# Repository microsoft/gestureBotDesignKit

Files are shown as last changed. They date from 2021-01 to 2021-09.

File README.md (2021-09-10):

##  [Microsoft Applied Robotics Research Library](https://microsoft.github.io/AppliedRoboticsResearchLibrary/)
### Open Source Samples for Service Robotics
  

# gestureBot Design Kit
Welcome! This gestureBot Design Kit repository  contains all the information needed to build both a virtual and physical desktop companion robot. Along with other tools in the Labanotation Suite, the gestureBot can be used to create and edit gestures documented in the Labanotation format and see them performed by a robot.  

A Windows 10 PC is required to run the software and the virtual robot. The physical robot can be built using a desktop 3D-printer and about **$350(USD)** in electronic servos and parts.

The kit contains a browser-based simulated robot with control software based on the [Robotis XL](https://www.robotis.us/dynamixel-xl-320/) series of servo motors. To construct a physical robot, it provides models for 3D-printable body-parts, a parts-list and purchase links for electronic components, and step-by-step assembly instructions. No soldering is required, but some manual skill is needed to mate small electronic connectors, manipulate small plastic rivets, and install miniature metal screws to assemble the body components.

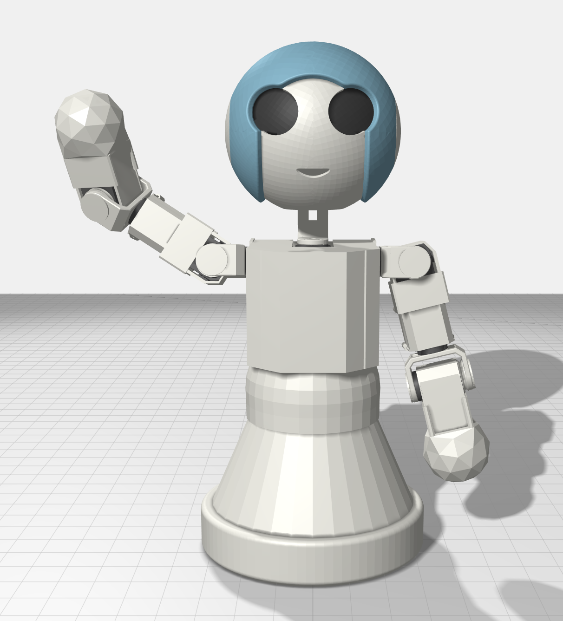
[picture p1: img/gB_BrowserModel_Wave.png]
Browser Model Wave


## What is the gestureBot and who might be interested in using this kit?
The gestureBot is a semi-humanoid service-robot capable of mimicking human gestures. Its purpose is to support research and education in the field of ***Human-Robot-Interaction (HRI)***. Its function is to physically and virtually render gestures stored in a digital Labanotation format. The designation "semi-humanoid" means that it has some but not all of the limbs and joints of a human form. The designation **"service-robot"** refers to a requirement that is designed to safely operate directly with humans, as opposed to an **"industrial-robot"** that usually repeats tasks within a cordoned-off safety zone. The gestureBot was adapted from a project originally created by interns working for Microsoft Research Asia. We've built on their work and put together this design kit to help students learn with a fun hand's-on project that provides exposure to key technologies used in service-robotics. Researchers in the field of HRI can use the kit to support experimentation in the use of gestures to enhance robot-to-human comunication.

No matter where your interest lies, we hope you find the gestureBot Design Kit a fun and easy way to work and learn in the field of robotics.

# How It Works
## System Diagram
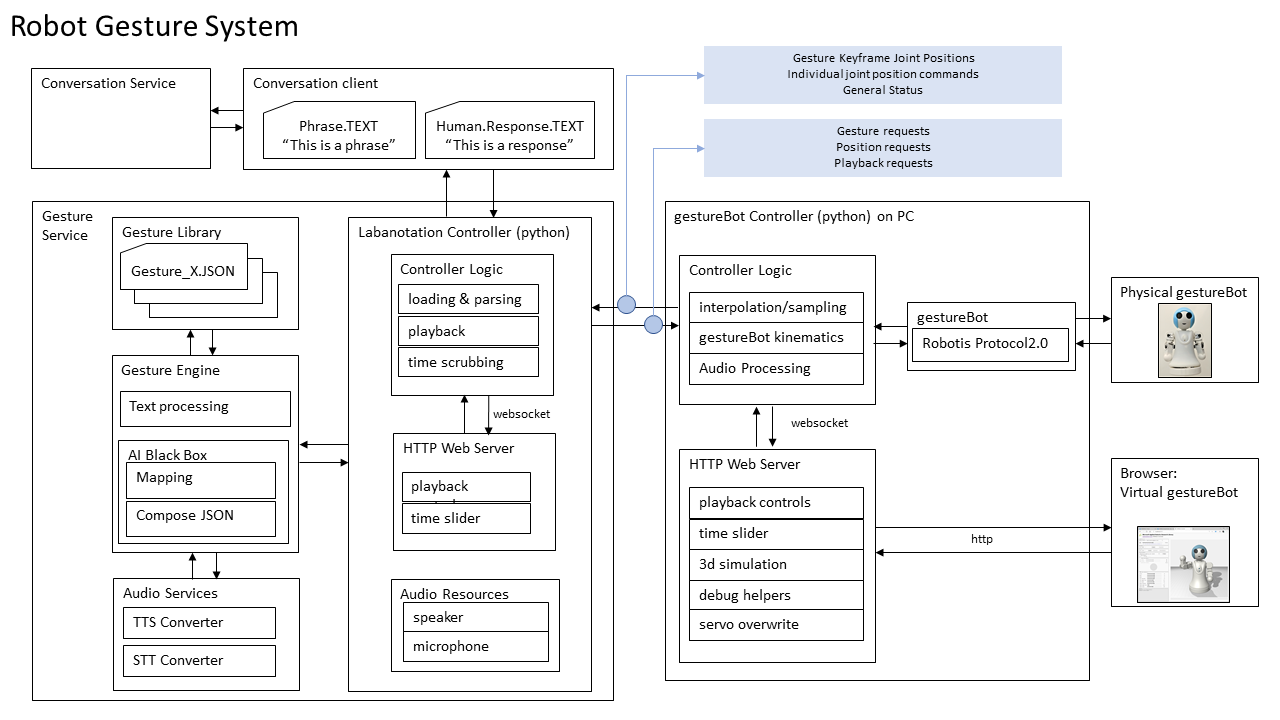
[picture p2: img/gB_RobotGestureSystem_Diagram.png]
gestureBot System Diagram


## System Modules:

### **Gesture Service**

#### **Labanotation Controller**
The Labanotation Controller reads .json files containing gestures described in Labanotation format, which are recordings of human gestural movements reduced to significant keyframes consisting of sequenced joint position and movement timing goals. Gesture selection and loading, as well as joint positional movements and their durations contained in the gestures, are requested by and sent to the gestureBot Controller module. The keyframes can also be transmitted under the control of simple play/pause commands and a scrubbing timeline with a browser-based UI available on **http port 8000**.

#### **Gesture Library**
The [**Gesture Library**](./src/Labanotation/README.md) is a database of gesture-concept pairs expressed in Labanotation format and stored as .json files. The data is directly accessed by the Gesture Engine.  The library includes a complete listing of the sample database including a video clip of each gesture performed by the gestureBot.

#### **Gesture Engine**
For humanoid robot performance, the Gesture Engine contains a software module constructed with Python and Google's neural network [**word2vec**](https://code.google.com/archive/p/word2vec/#!). It receives text phrases from the Labanotation Controller as input and returns corresponding gestures. Sample text phrases and gesture-concept pairs contained in the Gesture Library can be previewed by the system with a browser-based UI available on **http port 8002**.

### **gestureBot Controller**
The gestureBot Controller requests from the Labanotation Controller gestures to be loaded and played. Optionally, it will interpolate and insert interstitial keyframes between Labanotation keyframes in a gesture at a selectable sampling rate. It transforms goal positions and times contained in the keyframes into joint servo commands calculated using information specific to the the gestureBot's physical characteristics. It animates both the real and models of the robot using the servo commands and a library of virtual model assets. Finally, it provides a browser-based user interface on **http port 8001** for:
*   Selecting a Gesture-Concept .json input file for rendering
*   Optionally setting a sample rate for interstitial keyframe extrapolations between Labanotation keyframes
*   Optionally showing keyframe goal positions with "bone segments" within the browser-hosted model
*   Optionally hide cover components in the browser-hosted model
*   Direct override control for individual servos in the gestureBot
*   Previewing a gesture or movement in a simple simulator
*   Reporting application status with console messages

### **Real and Simulated gestureBots**
Both physical gestureBots and virtual models hosted in a browser connect to the gestureBot controller and receive movement commands as servo-control packets. The packets adhere to the [Robotis Dynamixel 2.0 Protocol](https://emanual.robotis.com/docs/en/dxl/x/xl320/). A packet is sent for each Labanotation and interstitial keyframe transmitted by the gestureBot Controller and contains individual goal positions and movement durations for each servo in the gestureBot.

# Install, Build and Run
- [Software Installation Instructions ](./src/Samples/gestureService_w2v/README.md) for the controller applications
- [Step-by-Step Instructions ](./hardware/README.md) for constructing a physical gestureBot

# Contributing
We think the gestureBot can be made to do much more than render gestures and we hope you will help it evolve! We have designed the hardware and software to be easy to understand and modify.
- Please read our [short and sweet coding guidelines](coding_guidelines.md).
- For big changes such as adding new feature or refactoring, [file an issue first](https://github.com/Microsoft/gestureBotDesignKit/issues).
- Use our [recommended development workflow](dev_workflow.md) to make changes and test it.
- Use [usual steps](https://akrabat.com/the-beginners-guide-to-contributing-to-a-github-project/) to make contributions just like other GitHub projects. If you are not familiar with Git Branch-Rebase-Merge workflow, please [read this first](http://shitalshah.com/p/git-workflow-branch-rebase-squash-merge/).

## Checklist
- Use same style and formatting as rest of code even if it's not your preferred one.
- Change any documentation that goes with code changes.
- Do not include OS specific header files or new 3rd party dependencies.
- Keep your pull request small, ideally under 10 files.
- Don't don't include large binary files.
- When adding new includes, make sure the dependency is absolutely necessary.
- Rebase your branch frequently with master (once every 2-3 days is ideal).
- Make sure your code compiles on Windows, Linux and OSX.

## FAQ

*   **Q** *Who should I contact regarding this repository?*

*   **A** Please create a Github issue or email [robosupp@microsoft.com](mailto:robosupp@microsoft.com) with any questions or feedback.

*   **Q** *How challenging is this project for children?*

*   **A** We think it depends on the child and how much support they receive!  We'd love to attract kids who love Minecraft and/or Legos, but we've shaped this project to be easily accessible to high-school and college STEM faculty looking for affordable lab projects, academic HRI researchers, and casual hobbyists.

*   **Q** *How does this project relate to Artificial Intelligence (AI)?*

*   **A** Physics-based simulation of real robots in virtual environments opens the door for the use of AI "brain" training using Reinforcement Learning tool-chains such as [Microsoft Bonsai](https://bons.ai).

## Citation

If you want to cite this work, please use the following bibtex code

```
@Article{Ikeuchi2018,
author="Ikeuchi, Katsushi
and Ma, Zhaoyuan
and Yan, Zengqiang
and Kudoh, Shunsuke
and Nakamura, Minako",
title="Describing Upper-Body Motions Based on Labanotation for Learning-from-Observation Robots",
journal="International Journal of Computer Vision",
year="2018",
month="Dec",
day="01",
volume="126",
number="12",
pages="1415--1429",
issn="1573-1405",
doi="10.1007/s11263-018-1123-1",
url="https://doi.org/10.1007/s11263-018-1123-1"
}
```

If you want to learn more about creating good readme files then refer the following [guidelines](https://docs.microsoft.com/en-us/azure/devops/repos/git/create-a-readme?view=azure-devops). You can also seek inspiration from the below readme files:
- [ASP.NET Core](https://github.com/aspnet/Home)
- [Visual Studio Code](https://github.com/Microsoft/vscode)
- [Chakra Core](https://github.com/Microsoft/ChakraCore)

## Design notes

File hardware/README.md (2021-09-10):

##  [Microsoft Applied Robotics Research Library](https://microsoft.github.io/AppliedRoboticsResearchLibrary/)
### Open Source Samples for Service Robotics
  

# gestureBot Construction Guide

The gestureBot is adapted from the [**Mini**](https://www.robotis.us/robotis-mini-intl/) robot kit from [**Robotis, Inc**](https://www.robotis.us) and the MSRAbot project created by interns at Microsoft Research Asia.
The information on this page will guide you through [**purchasing**](#purchased-parts) and [**printing**](#3d-printed-parts) parts, as well as [**step-by-step assembly**](#step-by-step-instructions) of the gestureBot.

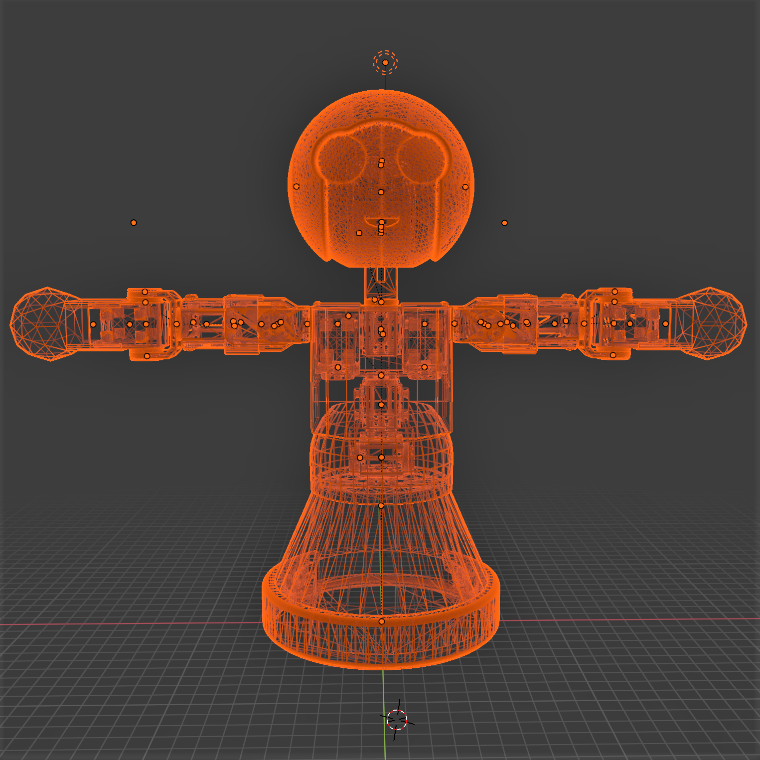
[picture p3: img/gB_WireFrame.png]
gestureBot wireframe


# Before you begin...
If you have experience in 3D printing and electronic assembly, we hope that you find this project relatively simple and straight-forward.  Once the parts are in-hand, the time required to complete the project won't be much more than it takes to print the 3D models.

If you are not experienced in these areas, one of the first things you'll learn is that desktop ***3D-printers are not a good source of instant gratification!***  Even the smallest of the models contained in this kit will take several hours to print, while some of the larger models take more than half a day.  With those time requirements in mind, we broke the procedures down into work sessions that fit along with the 3D print operations. Alternatively, a class of 5-10 students taking on this project might be successful with serial use of a single 3D printer and meeting once-a-week to perform the other assembly tasks.

An important feature of these instructions is their sequence. Following the steps in the sessions ***in order*** is key to preventing the need to disassemble an assembly in order to have access to cable pathways or screw and rivet holes.

# ***Safety Alert:***

We've found that a key to success in building this and other projects using 3D-printed plastic parts is to ***know your own strength***. Human hands can be more than strong enough to damage or destroy plastic parts, especially when muscle force is amplified by the leverage provided by a tool. For example, gripping a screwdriver with your fingers instead of the palm of your hand will limit the torque force you can apply with your muscles when driving a metal screw into a plastic servo horn (wheel). ***When applying muscle force with a tool against a plastic part, being aware of where the stationary force from your hand, body, or workbench is pushing back against your tool can avoid suddenly breaking the part and possibly causing injury.*** It is also helpful to use vision as well as force when tightening a screw. Paying attention to the closing gaps when turning a screw can help avoid stripping threads in the plastic and will make for stronger connections. A famous book that discusses this concept of "mechanic's feel" as well as other challenges in life is [***Zen and the Art of Motorcycle Maintenance: An Inquiry into Values***](https://hpb.com/products/zen-and-the-art-of-motorcycle-maintenance-an-inquiry-into-values-9780060589462) by Robert M. Persig.

## Requirements
Here are the physical things you'll need to build and use your gestureBot:

### PC
- x64 CPU
- Microsoft Windows 10
- USB3 port (USB2 can work in some cases)

### Tools
- 3D printer (we use an [Ultimaker3](https://ultimaker.com/3d-printers/ultimaker-3) with PLA filament)
- [Wire Stripper/Cutter](https://vetco.net/products/16awg-32awg-wire-stripper-cutter/plat-15005c)
- [small Phillips screwdriver (PH0)](https://vetco.net/products/general-tools-712010-precision-screwdriver-phillips-0)
- [small flat-blade screwdriver (2mm)](https://vetco.net/products/)
  - Alternative Screwdrivers:
    - [5 in 1 Precision Screwdriver](https://vetco.net/products/general-tools-spc606-jewelers-screwdriver-set-of-5)
    - [16 in 1 Precision Screwdriver](https://vetco.net/products/16-in-1-precision-screwdriver-set)
- pen and light-colored tape for labeling servo ID's

### Optional but Helpful Tools
- [Rivet Tool](https://www.robotis.us/tool-stl/)
- needle-nose pliers
- [Magnet (for easier screw driving)](https://vetco.net/products/3-4-round-magnet/son-pm550)
- 3mm drill bit, variable speed drill
- [3D-printing cleanup tools](https://www.matterhackers.com/articles/tools-of-the-trade-to-make-your-life-as-a-3d-print-master-much-simpler). A swivel deburring tool is especially useful.

## Parts List
### Purchased Parts
|**ID**|**Qty**|**Name & Purchase Link**|** . **|
|:--:|:--:|:---:|:---:|
|P1|12|[Robotis XL-320 Servo Motors (includes short connection cable)](https://www.robotis.us/dynamixel-xl-320/)||
|P2|1|[USB3 Hub with Power Supply](https://vetco.net/products/4-port-powered-usb-3-0-hub/vupn615)||
|P3|1|[Robotis OpenCM9.04c Servo Control Circuit Board](https://www.robotis.us/opencm9-04-c-with-onboard-xl-type-connectors/)|
|P4|1|[USB Terminal Block](https://vetco.net/products/usb-a-male-to-screw-terminal-breakout/cv051)|
|P5|1|[Short USB Cable (USB-A to USB-Micro)](https://vetco.net/products/usb-a-to-micro-usb-90-angle/)||
|P6|2|[Long (19cm) Servo Connection Cables](https://www.robotis.us/robot-cable-3p-xl-190mm-5pcs/)||
|P7|1|[6mm Plastic Rivets, (40) short (2-step) and (10) long (3-step)](https://www.robotis.us/robotis-mini-rivet-set/)||
|P7 (alternate)|1|[6mm Plastic Rivets (weaker but lower-cost, variety of colors)](https://www.robotis.us/rivet-set-rs-10/)||
|P8|1|[Screw Set](https://www.robotis.us/robotis-mini-screw-set/)|

### 3D Printed Parts
|**ID**|**Qty**|**Name & Model Link**|** . **|
|:--:|:--:|:--:|:---:|
|M1|1|[&nbsp; &nbsp; &nbsp; &nbsp; &nbsp; &nbsp; &nbsp; &nbsp; &nbsp; &nbsp; &nbsp; &nbsp; &nbsp; &nbsp; Base &nbsp; &nbsp; &nbsp;&nbsp; &nbsp;&nbsp; &nbsp;&nbsp; &nbsp;&nbsp; &nbsp; &nbsp; &nbsp; &nbsp; &nbsp; &nbsp; ](https://github.com/microsoft/gestureBotDesignKit/blob/main/hardware/3D_Print/gB_Base.stl)||
|M2|1|[Base Frame](https://github.com/microsoft/gestureBotDesignKit/blob/main/hardware/3D_Print/gB_BaseFrame.stl)||
|M3|1|[Bracket Cover (Rivet Side)](https://github.com/microsoft/gestureBotDesignKit/blob/main/hardware/3D_Print/gB_BracketCover_RivetSide.stl)||
|M4|1|[Bracket Cover (Screw Side)](https://github.com/microsoft/gestureBotDesignKit/blob/main/hardware/3D_Print/gB_BracketCover_ScrewSide.stl)||
|M5|2|[Ear](https://github.com/microsoft/gestureBotDesignKit/blob/main/hardware/3D_Print/gB_Ear.STL)||
|M6|1|[Eyes](https://github.com/microsoft/gestureBotDesignKit/blob/main/hardware/3D_Print/gB_Eyes.STL)||
|M7|1|[Face](https://github.com/microsoft/gestureBotDesignKit/blob/main/hardware/3D_Print/gB_Face.STL)||
|M8|2|[Hand](https://github.com/microsoft/gestureBotDesignKit/blob/main/hardware/3D_Print/gB_Neck.stl)||
|M9|1|[Head Frame](https://github.com/microsoft/gestureBotDesignKit/blob/main/hardware/3D_Print/gB_HeadFrame.stl)||
|M10|1|[Hip Cover](https://github.com/microsoft/gestureBotDesignKit/blob/main/hardware/3D_Print/gB_HipCover.stl)||
|M11|1|[Hood](https://github.com/microsoft/gestureBotDesignKit/blob/main/hardware/3D_Print/gB_Hood.stl)||
|M12|1|[Neck](https://github.com/microsoft/gestureBotDesignKit/blob/main/hardware/3D_Print/gB_Neck.stl)||
|M13|1|[Servo Cover](https://github.com/microsoft/gestureBotDesignKit/blob/main/hardware/3D_Print/gB_ServoCover.stl)||
|M14|2|[Servo Mount Plate](https://github.com/microsoft/gestureBotDesignKit/blob/main/hardware/3D_Print/gB_ServoMountPlate.stl)||
|M15|2|[Servo Side Cover](https://github.com/microsoft/gestureBotDesignKit/blob/main/hardware/3D_Print/gB_ServoSideCover.stl)||
|M16|2|[Servo Wheel](https://github.com/microsoft/gestureBotDesignKit/blob/main/hardware/3D_Print/gB_ServoWheel.stl)||
|M17|2|[Speaker](https://github.com/microsoft/gestureBotDesignKit/blob/main/hardware/3D_Print/gB_Speaker.stl)||
|M18|2|[Head Swing Bracket](https://github.com/microsoft/gestureBotDesignKit/blob/main/hardware/3D_Print/gB_SwingBracket_Head.stl)||
|M19|2|[Hip Swing Bracket](https://github.com/microsoft/gestureBotDesignKit/blob/main/hardware/3D_Print/gB_SwingBracket_Hip.stl)||
|M20|1|[Screw-Mount Swing Bracket](https://github.com/microsoft/gestureBotDesignKit/blob/main/hardware/3D_Print/gB_SwingBracket_ScrewMount.stl)||
|M21|1|[Upper Torso Back Cover](https://github.com/microsoft/gestureBotDesignKit/blob/main/hardware/3D_Print/gB_UpperTorsoBackCover.stl)||
|M22|1|[Upper Torso Front Cover](https://github.com/microsoft/gestureBotDesignKit/blob/main/hardware/3D_Print/gB_UpperTorsoFrontCover.stl)||
|M23|1|[Upper Torso Frame](https://github.com/microsoft/gestureBotDesignKit/blob/main/hardware/3D_Print/gB_UpperTorsoFrame.stl)||

# Step-by-Step Instructions
The 3D-printed parts are used to organize this project's task steps into sessions. 3D printing a part usually requires more time than is reasonable for a work session, often leaving the print operation to complete overnight as the most practical solution.

## Session 1: [Set Up the Servo Controller Electronics](./Session01.md)
In the first session we will begin the process of 3D-printing the gestureBot's plastic parts starting with the base frame while connecting the servo controller to the powered USB3 Hub and a single servo motor.

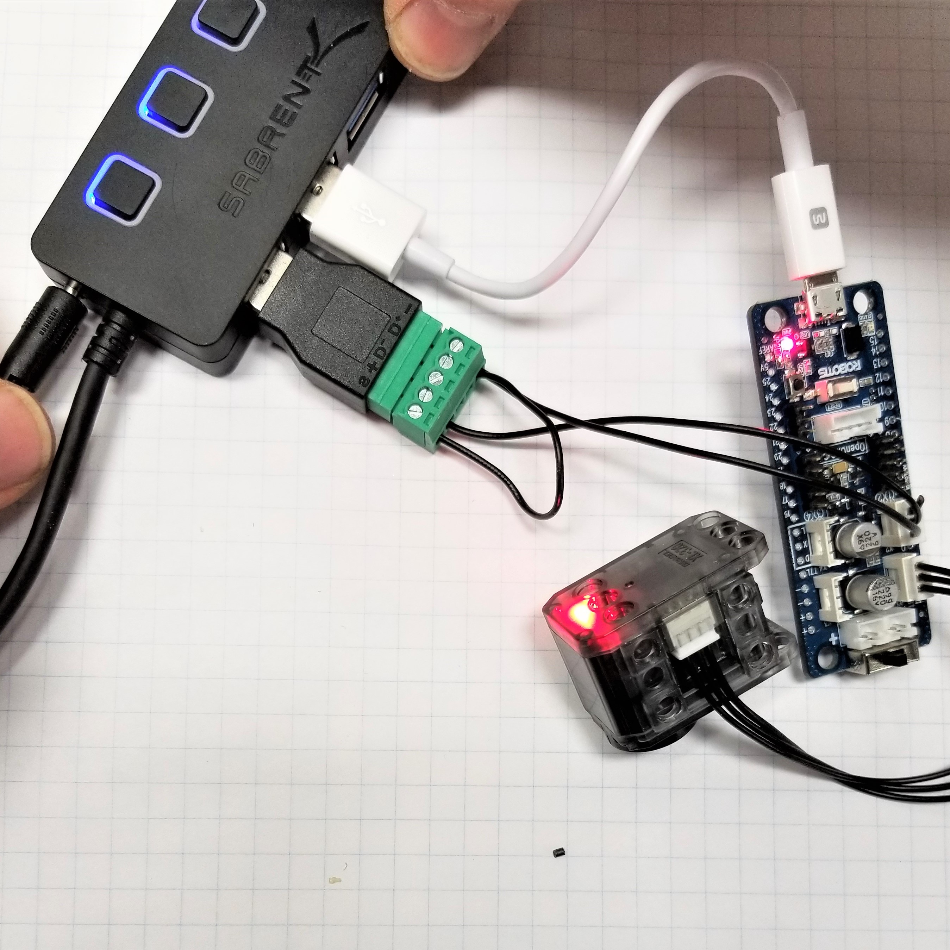
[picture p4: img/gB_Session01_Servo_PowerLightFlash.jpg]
Session 1 Complete


## Session 2: [Configure the Servos](./Session02.md)
In the second session we will 3D-print the gestureBot's torso components while establishing the communication network for our servo motors by connecting them one-by-one to the PC and using using the [Robotis Dynamixel Wizard 2.0](http://en.robotis.com/service/downloadpage.php?ca_id=10) application to program each with a unique ID.

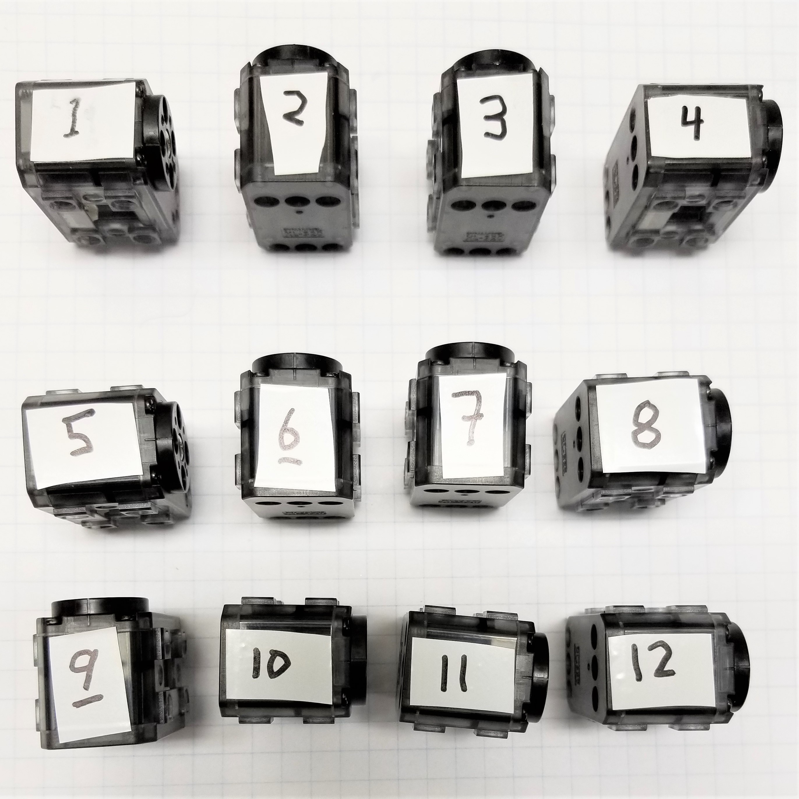
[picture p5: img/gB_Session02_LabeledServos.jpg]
Session 2 Complete


## Session 3: [Assemble the Torso](./Session03.md)
In the third session we will 3D-print the head components while assembling the gestureBot's torso.

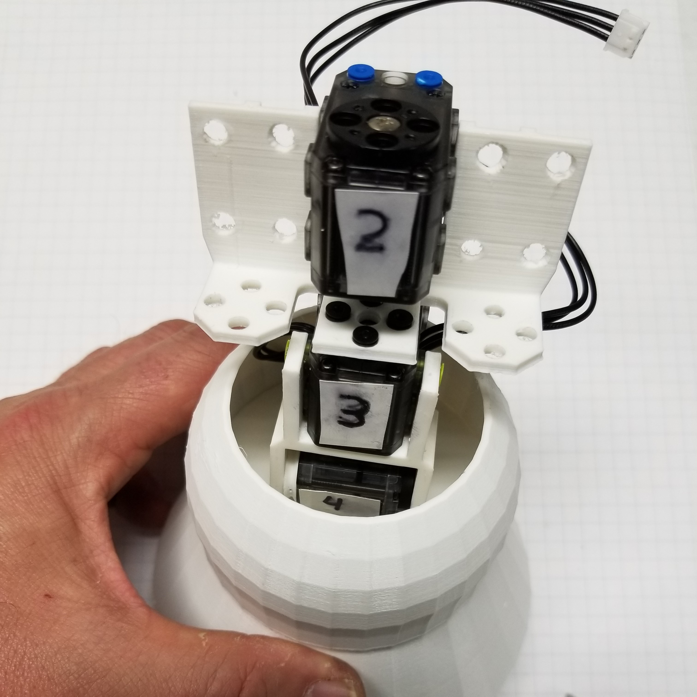
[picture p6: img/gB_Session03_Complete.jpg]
Session 3 Complete


## Session 4: [Assemble the Head Structure](./Session04.md)
In the fourth session we will 3D-print the components for both arms while assembling the structural components of the gestureBot's head.

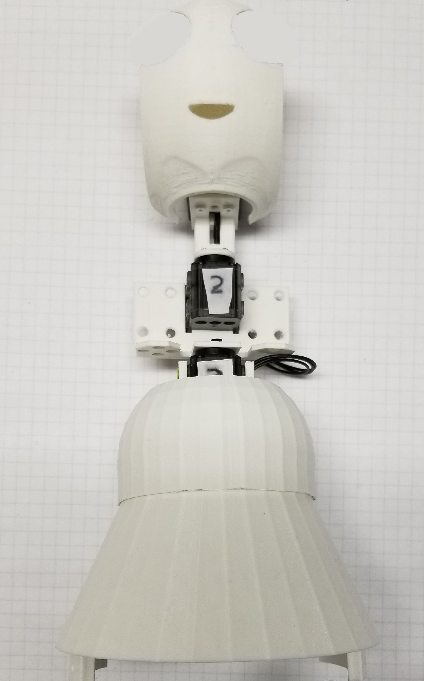
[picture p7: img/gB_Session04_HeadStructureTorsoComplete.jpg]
Session 4 Complete


## Session 5: [Assemble the Right Arm](./Session05.md)
In the fifth session we will 3D-print the base component while assembling the gestureBot's right arm.

## Session 6: [Assemble the Left Arm](./Session06.md)
In the sixth session we will 3D-print the eye and ear components (in an alternate color if desired) while assembling the gestureBot's left arm.

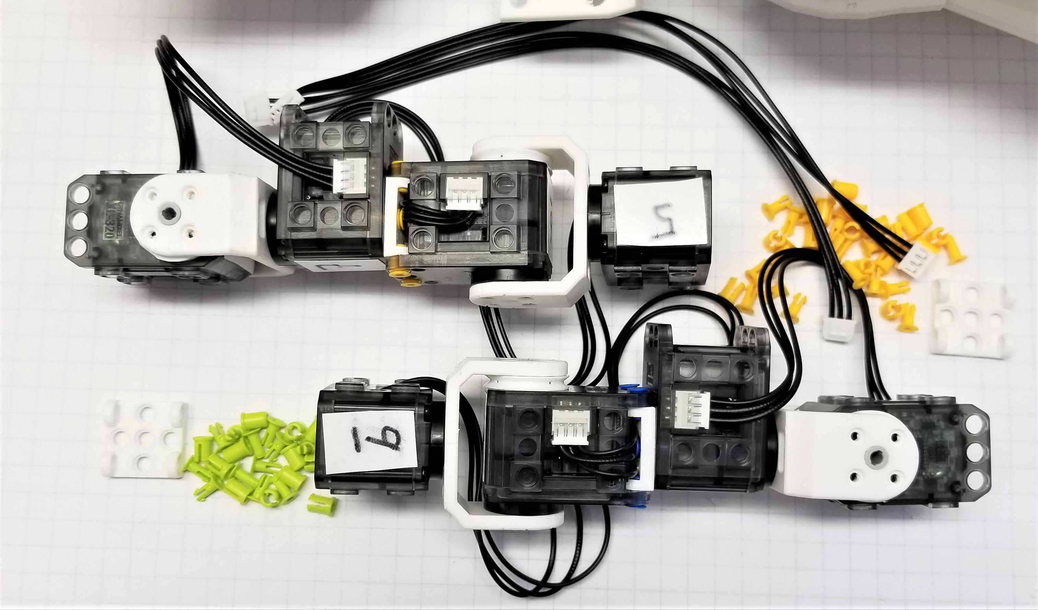
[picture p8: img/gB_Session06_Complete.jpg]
Session 6 Complete


## Session 7: [Attach the Arms and Test the Servos](./Session07.md)
In the seventh session we will 3D-print the hood component (in an alternate color if desired) while we attach the arms to the torso and test the servos using the [Robotis Dynamixel Wizard 2.0](https://www.robotis.us/dynamixel-management/) application.

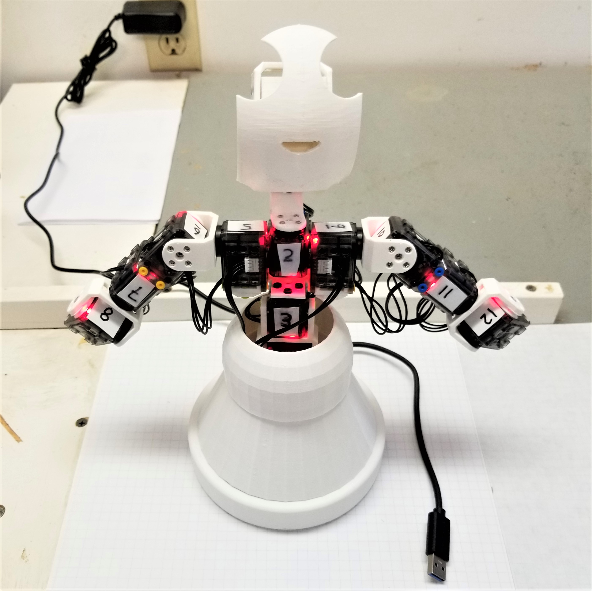
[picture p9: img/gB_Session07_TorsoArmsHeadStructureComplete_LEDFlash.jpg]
Session 7 Complete


## Session 8: [Complete the Head](./Session08.md)
In the eigth session we will 3D-print the hands and arm servo covers while we assemble the the head components.

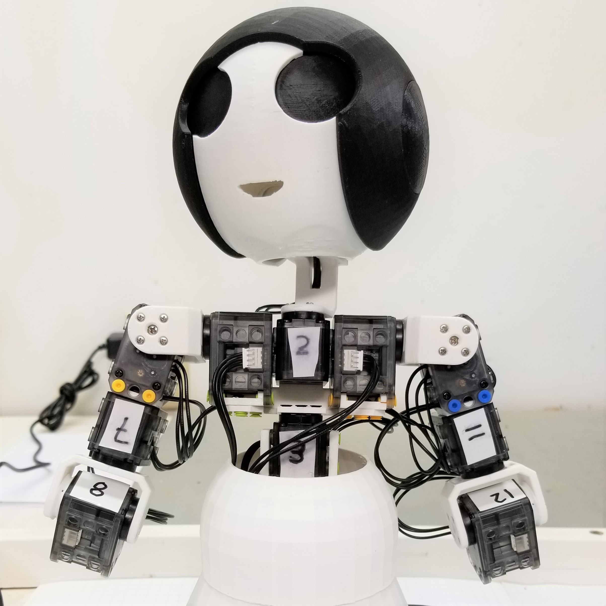
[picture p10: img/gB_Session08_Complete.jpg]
Session 8 Complete


## Session 9: [Install the Body Covers](./Session09.md)
In the ninth session we will 3D-print the torso front and back covers while we install the arm servo covers and hands.

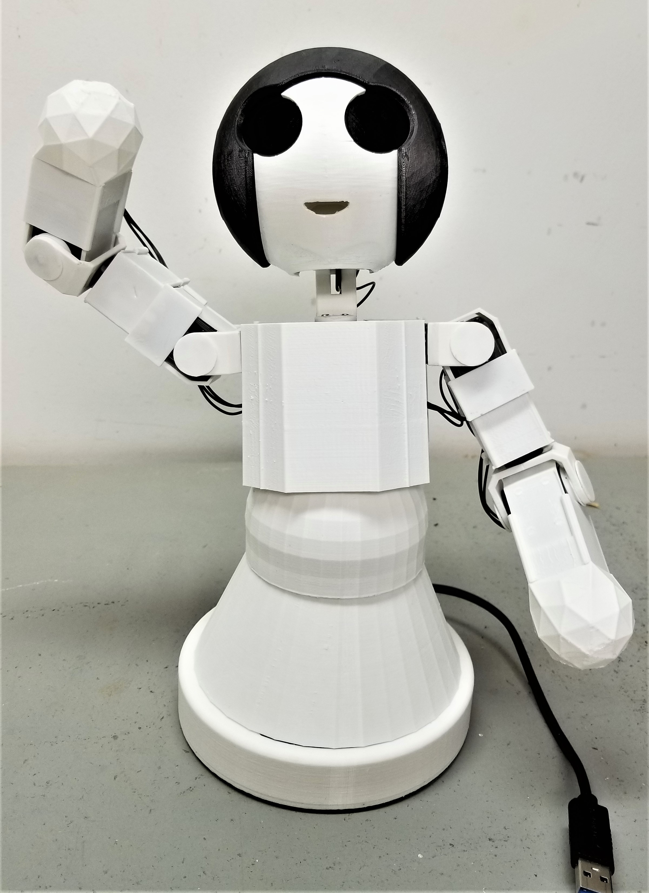
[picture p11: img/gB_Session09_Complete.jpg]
Session 9 Complete


## Session 10: [Run the Gesture Applications](./Session10.md)
In the tenth session we will 3D-print the torso cover components while we attach the hands and the arm servo covers. At this point the gestureBot will be ready to run the Labanotation Suite software applications. The torso covers can be attached as soon as they are finished printing.

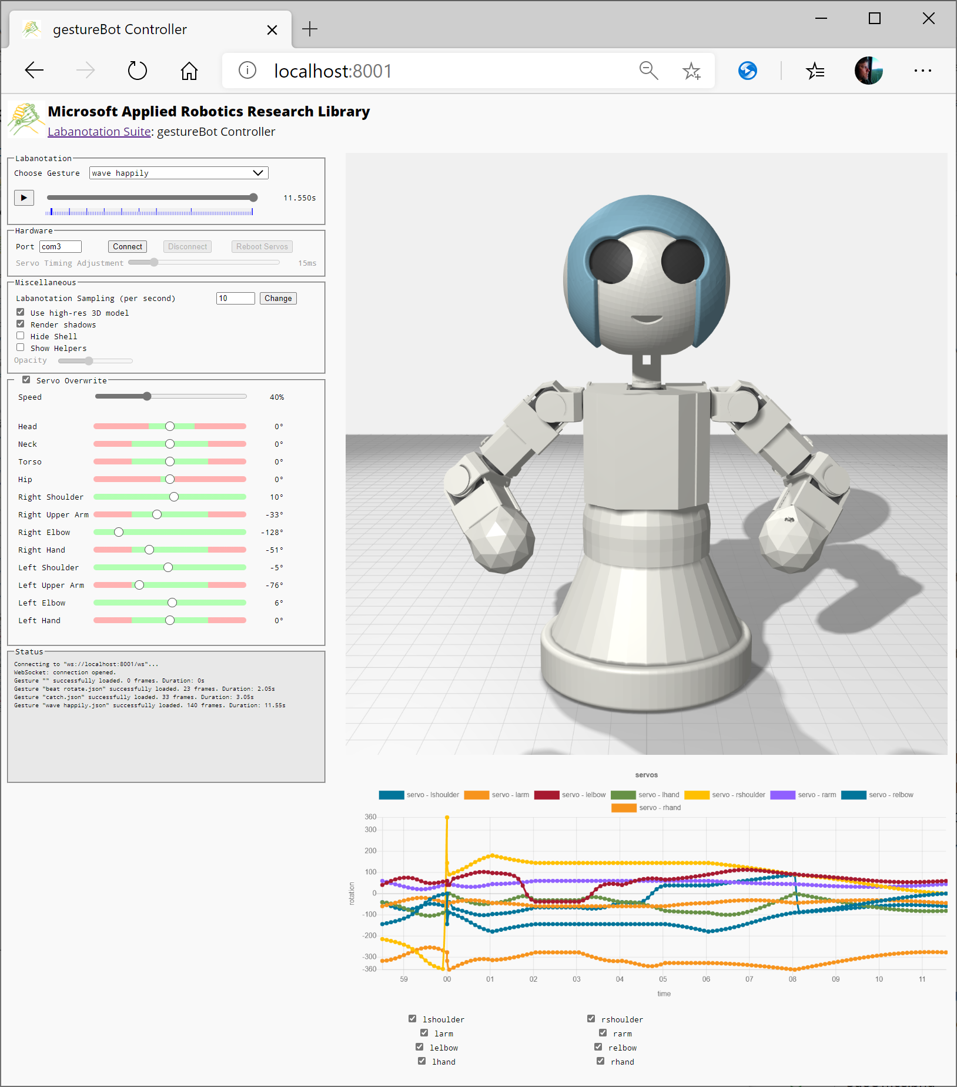
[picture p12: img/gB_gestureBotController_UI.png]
Session 10 Complete


# A last word...
Something to keep in mind is that this kit is designed to be changed and adapted. The 3D models are simple and lend themselves to modifications using such tools as [**Blender**](https://www.blender.org/). Additional devices such as cameras, microphones, and loudspeakers can be added using the two available USB ports in the base of the robot, as well as leveraging other devices and connections through the host PC. 

We can't wait to see what you come up with!

***--the Microsoft Applied Robotics Research Team***

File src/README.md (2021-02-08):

# [Microsoft Applied Robotics Research Library](https://github.com/microsoft/AppliedRoboticsResearchLibrary)
  

# Labanotation Suite: [gestureBot Design Kit](/README.md)

# **Source Code**

## [Labanotation](/src/Labanotation)
The Labanotation folder contains gesture data files expressed in Labanotation and stored in .json format

## [Libraries](/src/Libraries)
The Libraries folder contains source code for component software modules used by this project's sample applications.

## [Samples](/src/Samples)
The Samples folder contains example application source code for the gestureBot project.

## [Tools](/src/Tools)
The Tools folder contains utility application source code for the gestureBot project.

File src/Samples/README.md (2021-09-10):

##  [Microsoft Applied Robotics Research Library](https://microsoft.github.io/AppliedRoboticsResearchLibrary/)
### Open Source Samples for Service Robotics
  

# Software Samples

## [Gesture Service](https://github.com/microsoft/gestureBotDesignKit/tree/main/src/Samples/gestureService_w2v)
The Gesture Service sample source code in 'gestureService_w2v.pyproj' demonstrates how to instantiate and run all of the software modules in the project together as a system: 
- Gesture Service
  - Labanotation controller
  - Gesture Engine based on Google's [word2vec](https://code.google.com/archive/p/word2vec/#!)
  - Gesture Library
- gestureBot controller

## [gestureBot](https://github.com/microsoft/gestureBotDesignKit/tree/main/src/Samples/gestureBot)
The gestureBot sample source code in 'gestureBot.pyproj' demonstrates how to instantiate and run the minimum software modules required to control a physical robot and have it perform gestures from ghe Gesture Library:
- Gesture Service
  - Labanotation controller
  - Gesture Library
- gestureBot controller

## [Simple](https://github.com/microsoft/gestureBotDesignKit/tree/main/src/Samples/Simple)
The sample source code in 'Simple.pyproj' demonstrates how to instantiate and run the Labanotation Controller software module by itself.

## [gestureBotSetLimits](https://github.com/microsoft/gestureBotDesignKit/tree/main/src/Samples/gestureBotSetLimits)
The sample source code in 'gestureBotSetLimits.pyproj' demonstrates how to send configuration commands to the servos using the Robotis Dynamixel 2.0 Protocol. This sample is provided as part of the physical gestureBot construction procedures to set specific rotation limits on particular servos. These limits can help prevent damage caused by incorrect commands or code errors resulting in physical collisions of the gestureBot body components. ***To run this sample, a complete physical gestureBot robot connected to the PC's USB port is required.***

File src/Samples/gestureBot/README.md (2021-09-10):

##  [Microsoft Applied Robotics Research Library](https://microsoft.github.io/AppliedRoboticsResearchLibrary/)
### Open Source Samples for Service Robotics
  

# gestureBot Sample
The gestureBot sample source code in 'gestureBot.pyproj' demonstrates how to instantiate and run the software modules required to control a physical robot and have it perform gestures from ghe Gesture Library:
- Gesture Service
  - Labanotation controller
  - Gesture Library
- gestureBot controller

***Note: this sample does not include the Gesture Engine module, which is included in the [gestureService_w2v.pyroj](/src/Samples/gestureService_w2v) sample at src/Samples/gestureService_w2v.***

# Software Installation
The sample 'gestureBot' source code depends on a number of open-source Python libraries. This section provides instructions for installing and operating the software.

## Tested System Software
We used the following software versions to test the Gesture Service samples:
- Windows 10 (Version 2004, 64-bit) **or** Linux (Ubuntu18.04, 64-bit)
- Microsoft Edge Browser (Version 87.0.664.66, 64-bit)
- Git client [*(Comes with Microsoft Visual Studio Code)*](https://code.visualstudio.com/Download)
- [Python 3.7.8](https://www.python.org/downloads/release/python-378/)

### Python Modules
* The following modules are listed in a requirements.txt file for easy installation:
```
numpy==1.19.3
scipy==1.5.2
tornado==4.5.2
opencv-python==4.4.0.46
pyserial==3.4
msgpack-rpc-python==0.4.1
gensim==3.8.3
nltk==3.5
dynamixel_sdk==3.7.31
```

## Installation Instructions
For Windows or Linux, the following instructions will guide you through the installation of code and assets comprising the gestureBot Design Kit as well as dependent external software.

If not already on your PC, download and run the following installers:
- Python 3.7.8:
 [https://www.python.org/downloads/release/python-378/](https://www.python.org/downloads/release/python-378/)

- PIP:
[https://bootstrap.pypa.io/get-pip.py](https://bootstrap.pypa.io/get-pip.py)

From a [**cmd.exe**](C:\WINDOWS\system32\cmd.exe), bash, or other terminal shell:
*   Create a folder for the installation in any convenient location and make it the current directory:
```
> mkdir [folder path]
> cd [folder path]]
```
- Clone the repository:
```
> git clone --recursive https://github.com/microsoft/gestureBotDesignKit
```
- Run these commands to download and install required python software modules:

***Tip:*** on some systems, earlier versions of python (such as python 2.7) may already be installed with a need to keep them as they are. In this case, it may be required to set a system variable that creates a path to the new installation with a link such as "python37".

```
> python get-pip.py
> python -m pip install -r requirements.txt
```

The following examples assume the repository was downloaded to a folder:
``` 
c:\Users\robotics\github_repos\gestureBotDesignKit\
```

Following is an example launch session preceded by a check to insure the correct version of Python 3.7.8 is invoked:
```
C:\Users\robotics>python
Python 3.7.8 (tags/v3.7.8:4b47a5b6ba, Jun 28 2020, 08:53:46) [MSC v.1916 64 bit (AMD64)] on win32
Type "help", "copyright", "credits" or "license" for more information.
>>> quit()
>
> cd \Users\robotics\github_repos\gestureBotDesignKit\src\Samples\gestureBot

C:\Users\robotics\github_repos\gestureBotDesignKit\src\Samples\gestureBot>python37 main.py
Labanotation Sample: gestureBot v1.00.0178

Http controller started on http://localhost:8000.
loaded 'Ges02_balancinghands.total.json': 10 frames. Performance duration: 5.347s
gestureBot1: creating key frames with a sampling rate of 0.100s per sample...
Http gestureBot1 started on http://localhost:8001.
Ready.
```
# Sample Operations
The two user-interfaces (UI) in this sample can be run in a browser window on the local machine with the localhost URL's provided in each section below.

***Tip:*** If 'localhost' is not a mapped name on the PC, it can be substituted with the PC's local IP address. Also, remote control can be achieved on the local network segment by using the PC's IP address in a browser on a different PC.

## Labanotation Controller UI
[http://localhost:8000](http://localhost:8000)
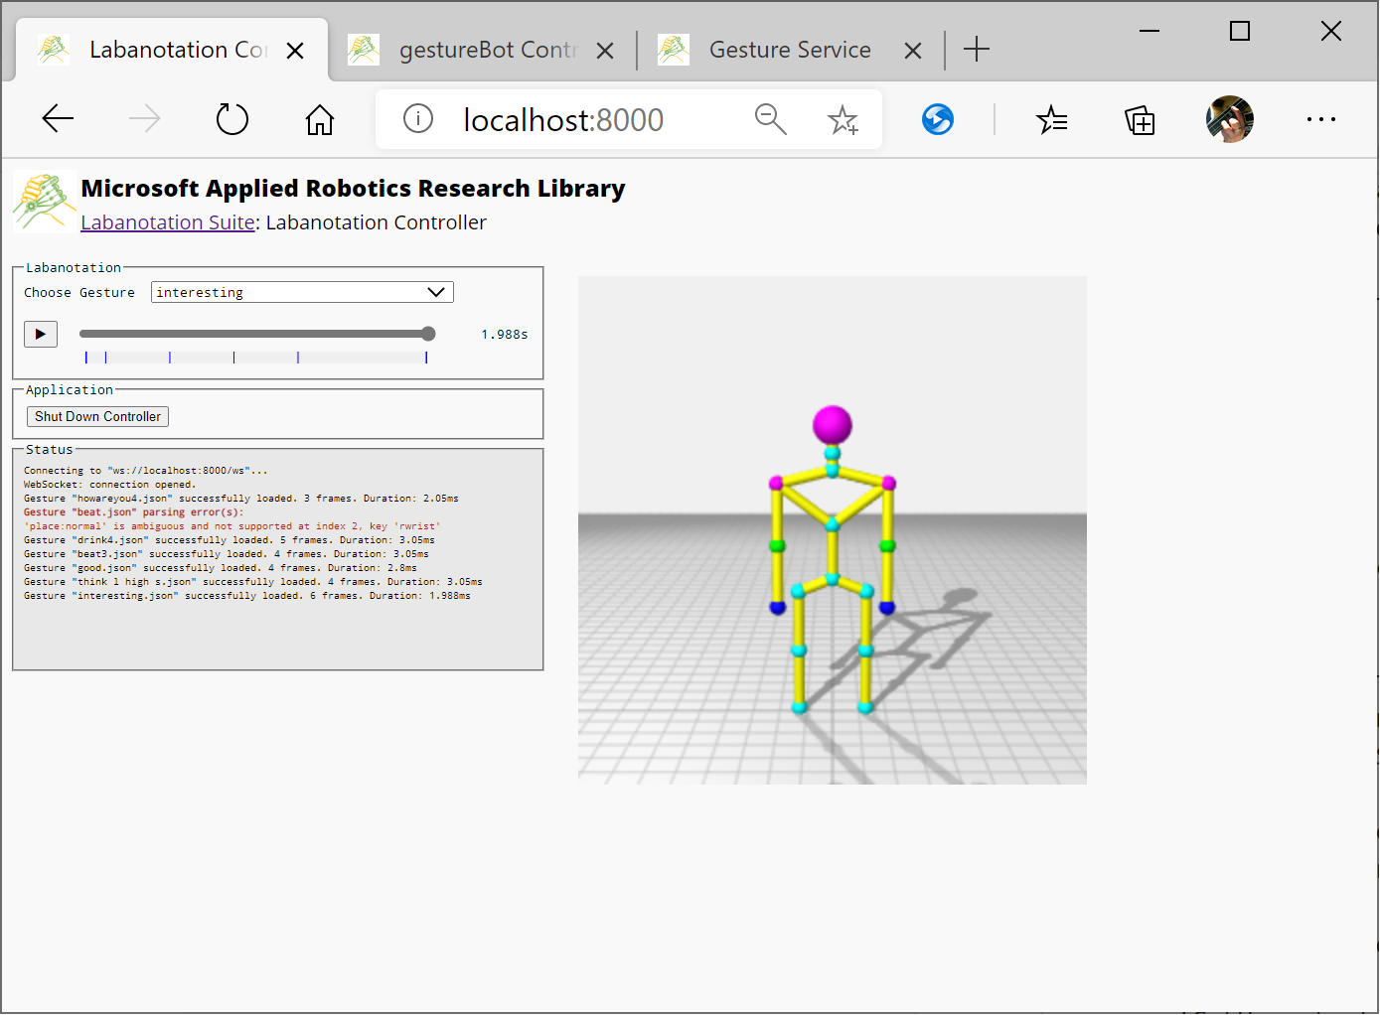
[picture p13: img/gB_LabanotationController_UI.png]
Labanotation Controller UI


## gestureBot Controller UI
[http://localhost:8001](http://localhost:8001)
gestureBot Controller UI

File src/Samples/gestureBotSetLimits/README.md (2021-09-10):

##  [Microsoft Applied Robotics Research Library](https://microsoft.github.io/AppliedRoboticsResearchLibrary/)
### Open Source Samples for Service Robotics
  

# gestureBotSetLimits Sample
The sample source code in 'gestureBotSetLimits.pyproj' demonstrates how to send configuration commands to the servos using the Robotis Dynamixel 2.0 Protocol. This sample is provided as part of the physical gestureBot construction procedures to set specific rotation limits on particular servos. These limits can help prevent damage caused by incorrect commands or code errors resulting in physical collisions of the gestureBot body components. ***To run this sample, a complete physical gestureBot robot connected to the PC's USB port is required.*** 

# Software Installation
The sample 'gestureBotSetLimites' source code depends on a number of open-source Python libraries. This section provides instructions for installing and operating the software.

## Tested System Software
We used the following software versions to test the Gesture Service samples:
- Windows 10 (Version 2004, 64-bit) **or** Linux (Ubuntu18.04, 64-bit)
- Microsoft Edge Browser (Version 87.0.664.66, 64-bit)
- Git client [*(Comes with Microsoft Visual Studio Code)*](https://code.visualstudio.com/Download)
- [Python 3.7.8](https://www.python.org/downloads/release/python-378/)

### Python Modules
- The following modules are listed in a requirements.txt file for easy installation:
```
numpy==1.19.3
scipy==1.5.2
tornado==4.5.2
opencv-python==4.4.0.46
pyserial==3.4
msgpack-rpc-python==0.4.1
gensim==3.8.3
nltk==3.5
dynamixel_sdk==3.7.31
```

## Installation Instructions
For Windows or Linux, the following instructions will guide you through the installation of code and assets comprising the gestureBot Design Kit as well as dependent external software.

If not already on your PC, download and run the following installers:
- Python 3.7.8:
 [https://www.python.org/downloads/release/python-378/](https://www.python.org/downloads/release/python-378/)

- PIP:
[https://bootstrap.pypa.io/get-pip.py](https://bootstrap.pypa.io/get-pip.py)

From a [**cmd.exe**](C:\WINDOWS\system32\cmd.exe), bash, or other terminal shell:
- Create a folder for the installation in any convenient location and make it the current directory:
```
> mkdir [folder path]
> cd [folder path]]
```
- Clone the repository:
```
> git clone --recursive https://github.com/microsoft/gestureBotDesignKit
```
- Run these commands to download and install required python software modules:

***Tip:*** on some systems, earlier versions of python (such as python 2.7) may already be installed with a need to keep them as they are. In this case, it may be required to set a system variable that creates a path to the new installation with a link such as "python37".

```
> python get-pip.py
> python -m pip install -r requirements.txt
```

- Using Microsoft Visual Code or any text editor, open the file in the repository folder:
\gestureBotDesignKit\src\Samples\gestureBotSetLimits\main.py

- In **line 50**, change the value to match the serial port noted earlier for your gestureBot. For example:
```
    self.comPort = "com4"
```
***Tip:*** If needed, the serial port can be looked up in Windows Device Manager as shown at the end of [Session 1](/docs_images/Session01.md).

# Sample Operations
The following example run session starts with a check that the correct verion of Python (3.7.8) is invoked and assumes the repository was downloaded to a folder:
``` 
c:\Users\robotics\github_repos\gestureBotDesignKit\
```
The example session:
```
C:\Users\robotics>python
Python 3.7.8 (tags/v3.7.8:4b47a5b6ba, Jun 28 2020, 08:53:46) [MSC v.1916 64 bit (AMD64)] on win32
Type "help", "copyright", "credits" or "license" for more information.
>>quit()
>
> cd \Users\robotics\github_repos\gestureBotDesignKit\src\Samples\gestureBotSetLimits\

C:\Users\robotics\github_repos\gestureBotDesignKit\src\Samples\gestureBotSetLimits>python main.py
gestureBot: connecting to port 'com4'...
ID: 1: setting CW angle limit to -70 (272)
ID: 1: setting CCW angle limit to 50 (682)
ID: 2: setting CW angle limit to -91 (201)
ID: 2: setting CCW angle limit to 91 (821)
gestureBot: disconnecting from port 'com4'...
```
***Tip:*** In the future, if you modify your gestureBot and want to set different safety limits, this code provides an example in the **run()** function starting at **line 270**.

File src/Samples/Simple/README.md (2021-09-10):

##  [Microsoft Applied Robotics Research Library](https://microsoft.github.io/AppliedRoboticsResearchLibrary/)
### Open Source Samples for Service Robotics
  

# Simple Sample
The sample source code in 'Simple.pyproj' demonstrates how to instantiate and run the Labanotation Controller software module by itself.

# Software Installation
The sample 'Simple' source code depends on a number of open-source Python libraries. This section provides instructions for installing and operating the software.

## Tested System Software
We used the following software versions to test the Gesture Service samples:
- Windows 10 (Version 2004, 64-bit) **or** Linux (Ubuntu18.04, 64-bit)
- Microsoft Edge Browser (Version 87.0.664.66, 64-bit)
- Git client [*(Comes with Microsoft Visual Studio Code)*](https://code.visualstudio.com/Download)
- [Python 3.7.8](https://www.python.org/downloads/release/python-378/)

### Python Modules
- The following modules are listed in a requirements.txt file for easy installation:
```
numpy==1.19.3
scipy==1.5.2
tornado==4.5.2
opencv-python==4.4.0.46
pyserial==3.4
msgpack-rpc-python==0.4.1
gensim==3.8.3
nltk==3.5
dynamixel_sdk==3.7.31
```
## Installation Instructions
For Windows or Linux, the following instructions will guide you through the installation of code and assets comprising the gestureBot Design Kit as well as dependent external software.

If not already on your PC, download and run the following installers:
- Python 3.7.8:
 [https://www.python.org/downloads/release/python-378/](https://www.python.org/downloads/release/python-378/)

- PIP:
[https://bootstrap.pypa.io/get-pip.py](https://bootstrap.pypa.io/get-pip.py)

From a [**cmd.exe**](C:\WINDOWS\system32\cmd.exe), bash, or other terminal shell:
- Create a folder for the installation in any convenient location and make it the current directory:
```
> mkdir [folder path]
> cd [folder path]]
```
- Clone the repository:
```
> git clone --recursive https://github.com/microsoft/gestureBotDesignKit
```
- Run these commands to download and install required python software modules:

***Tip:*** on some systems, earlier versions of python (such as python 2.7) may already be installed with a need to keep them as they are. In this case, it may be required to set a system variable that creates a path to the new installation with a link such as "python37".

```
> python get-pip.py
> python -m pip install -r requirements.txt
```
The following examples assume the repository was downloaded to a folder:
``` 
c:\Users\robotics\github_repos\gestureBotDesignKit\
```
Following is an example run session preceded by a check to insure the correct version of Python 3.7.8 is invoked:
```
C:\Users\robotics>python
Python 3.7.8 (tags/v3.7.8:4b47a5b6ba, Jun 28 2020, 08:53:46) [MSC v.1916 64 bit (AMD64)] on win32
Type "help", "copyright", "credits" or "license" for more information.
>>> quit()
>
> cd \Users\robotics\github_repos\gestureBotDesignKit\src\Samples\Simple

C:\Users\dbaum\source\github_repos\gestureBotDesignKit\src\Samples\Simple>python main.py
Labanotation Sample: Simple v1.00.0178

Http controller started on http://localhost:8000.
loaded 'Ges02_balancinghands.total.json': 10 frames. Performance duration: 5.347s
Ready.

```
# Sample Operations
The user-interface (UI) in this sample can be run in a browser window on the local machine with the localhost URL's provided in each section below.

***Tip:*** If 'localhost' is not a mapped name on the PC, it can be substituted with the PC's local IP address. Also, remote control can be achieved on the local network segment by using the PC's IP address in a browser on a different PC.

## Labanotation Controller UI
[http://localhost:8000](http://localhost:8000)
Labanotation Controller UI

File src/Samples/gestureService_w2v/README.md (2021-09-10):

##  [Microsoft Applied Robotics Research Library](https://microsoft.github.io/AppliedRoboticsResearchLibrary/)
### Open Source Samples for Service Robotics
  

# Gesture Service System Sample

The Gesture Service sample source code in 'gestureService_w2v.pyproj' demonstrates how to instantiate and run all of the software modules in the project together:
- Gesture Service
  - Labanotation controller
  - Gesture Engine based on Google word2vec
  - Gesture Library
- gestureBot controller

## Software Installation
The sample 'gestureService_w2v' source code depends on a number of open-source Python libraries. This section provides instructions for installing and operating the software.

### Tested System Software
We used the following software versions to test the Gesture Service samples:
- Windows 10 (Version 2004, 64-bit) **or** Linux (Ubuntu18.04, 64-bit)
- Microsoft Edge Browser (Version 87.0.664.66, 64-bit)
- Git client [*(Comes with Microsoft Visual Studio Code)*](https://code.visualstudio.com/Download)
- [Python 3.7.8](https://www.python.org/downloads/release/python-378/)

### Python Modules
- The following modules are listed in a requirements.txt file for easy installation:
```
numpy==1.19.3
scipy==1.5.2
tornado==4.5.2
opencv-python==4.4.0.46
pyserial==3.4
msgpack-rpc-python==0.4.1
gensim==3.8.3
nltk==3.5
dynamixel_sdk==3.7.31
```

### Installation Instructions
For Windows or Linux, the following instructions will guide you through the installation of code and assets comprising the gestureBot Design Kit as well as dependent external software.

If not already on your PC, download and run the following installers:
- Python 3.7.8:
 [https://www.python.org/downloads/release/python-378/](https://www.python.org/downloads/release/python-378/)

- PIP:
[https://bootstrap.pypa.io/get-pip.py](https://bootstrap.pypa.io/get-pip.py)

From a [**cmd.exe**](C:\WINDOWS\system32\cmd.exe), bash, or other terminal shell:
- Create a folder for the installation in any convenient location and make it the current directory:
```
> mkdir [folder path]
> cd [folder path]]
```
- Clone the repository:
```
> git clone --recursive https://github.com/microsoft/gestureBotDesignKit
```
- Run these commands to download and install required python software modules:

***Tip:*** on some systems, earlier versions of python (such as python 2.7) may already be installed with a need to keep them as they are. In this case, it may be required to set a system variable that creates a path to the new installation with a link such as "python37".

```
> python get-pip.py
> python -m pip install -r requirements.txt
```

The following examples assume the repository was downloaded to a folder:
``` 
c:\Users\robotics\github_repos\gestureBotDesignKit\
```
To provide a sample Gesture Engine implementation, Google's neural network [word2vec](https://code.google.com/archive/p/word2vec/#!) is used and available at this link: https://code.google.com/archive/p/word2vec/#!

  To install, download the [GoogleNews-vectors-negative300.bin](https://drive.google.com/file/d/0B7XkCwpI5KDYNlNUTTlSS21pQmM/edit?usp=sharing) binary file and unzip it into the example Library folder as follows:
```
C:\Users\robotics\github_repos\gestureBotDesignKit\src\Libraries\gestureService_w2v\GoogleNews-vectors-negative300.bin
```
## Run the System
Following is an example run session preceded by a check to insure the correct version of Python 3.7.8 is invoked:
```
C:\Users\robotics>python
Python 3.7.8 (tags/v3.7.8:4b47a5b6ba, Jun 28 2020, 08:53:46) [MSC v.1916 64 bit (AMD64)] on win32
Type "help", "copyright", "credits" or "license" for more information.
>>quit()
>
> cd \Users\robotics\github_repos\gestureBotDesignKit\src\Samples\gestureService_w2v

C:\Users\robotics\github_repos\gestureBotDesignKit\src\Samples\gestureService_w2v>python main.py
Labanotation Sample: gesture Service v1.00.0178

Http controller started on http://localhost:8000.
gestureBot: creating key frames with a sampling rate of 0.100s per sample...
Http gestureBot started on http://localhost:8001.
loading 'C:\Users\robotics\github_repos\gestureBotDesignKit\src\Libraries\gestureService_w2v\GoogleNews-vectors-negative300.bin'...
word vector database took 19.139934062957764 seconds to load...
Loading and parsing labanotation gesture dictionary...
Http application started on http://localhost:8002.
Ready.
```
## System Operations
The three user-interfaces (UI) in this sample can be run in a browser window on the local machine with the localhost URL's provided in each section below.

***Tip:*** If 'localhost' is not a mapped name on the PC, it can be substituted with the PC's local IP address. Also, remote control can be achieved on the local network segment by using the PC's IP address in a browser on a different PC.

### Labanotation Controller UI
[http://localhost:8000](http://localhost:8000)
Labanotation Controller UI

### Gesture Service UI
[http://localhost:8002](http://localhost:8002)
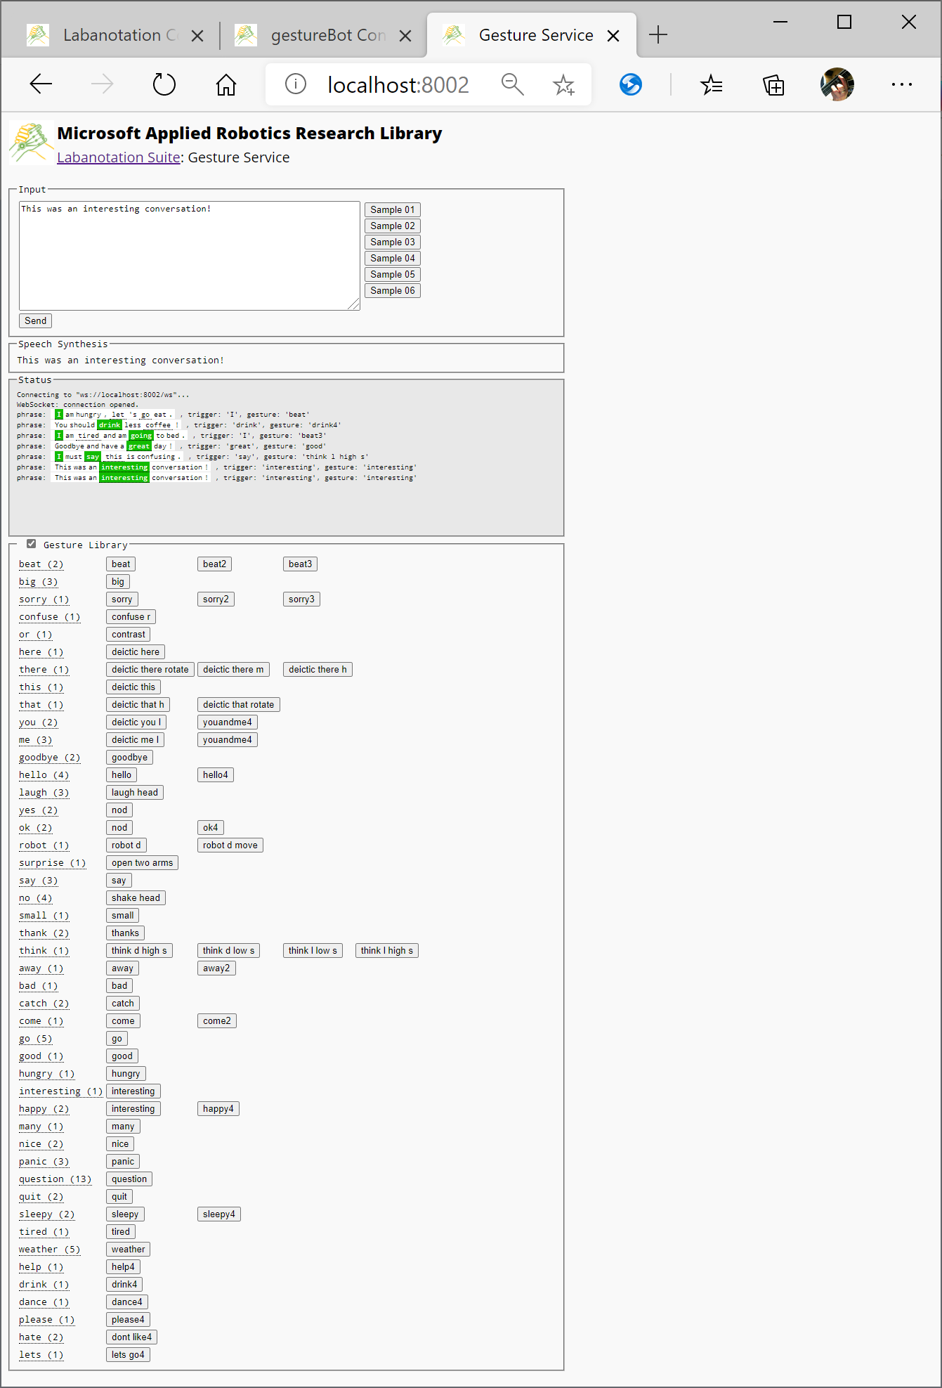
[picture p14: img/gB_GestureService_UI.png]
Gesture Service UI


### gestureBot Controller UI
[http://localhost:8001](http://localhost:8001)
gestureBot Controller UI

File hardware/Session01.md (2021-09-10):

##  [Microsoft Applied Robotics Research Library](https://microsoft.github.io/AppliedRoboticsResearchLibrary/)
### Open Source Samples for Service Robotics
  
# [gestureBot Construction Guide](../hardware/README.md)

## **Session 1:** Set Up the Servo Controller Electronics
In this first session we will begin the process of 3D-printing robot plastic parts starting with the base frame which will be used in Session 2. Then, we will connect the servo controller to the powered USB3 Hub and a single servo motor.

### Parts: 
- (2) servos and their included 130mm cables
- USB Terminal Block
- USB3 Hub with Power Supply
- Servo Controller

### Tools: 
- wire strippers/cutters
- 2mm screwdriver

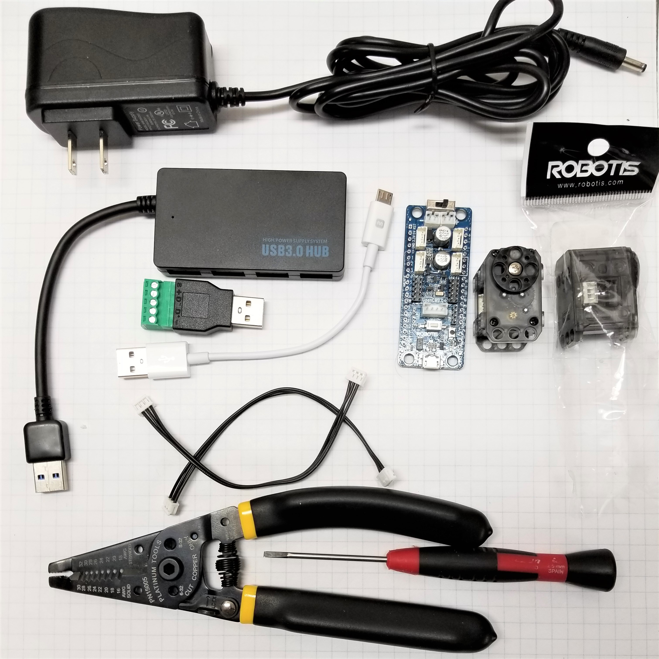
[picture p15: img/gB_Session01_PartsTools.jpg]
Session01 parts and tools


### **Procedure:**

#### **First, start 3D-printing the parts required for the next session:**
- [Base Frame](https://github.com/microsoft/gestureBotDesignKit/blob/main/hardware/3D_Print/gB_BaseFrame.stl)

#### **Second, connect the controller and Terminal Block to the USB Hub:**

- From two servo packages, remove the short connection cables and servos then set one servo aside.
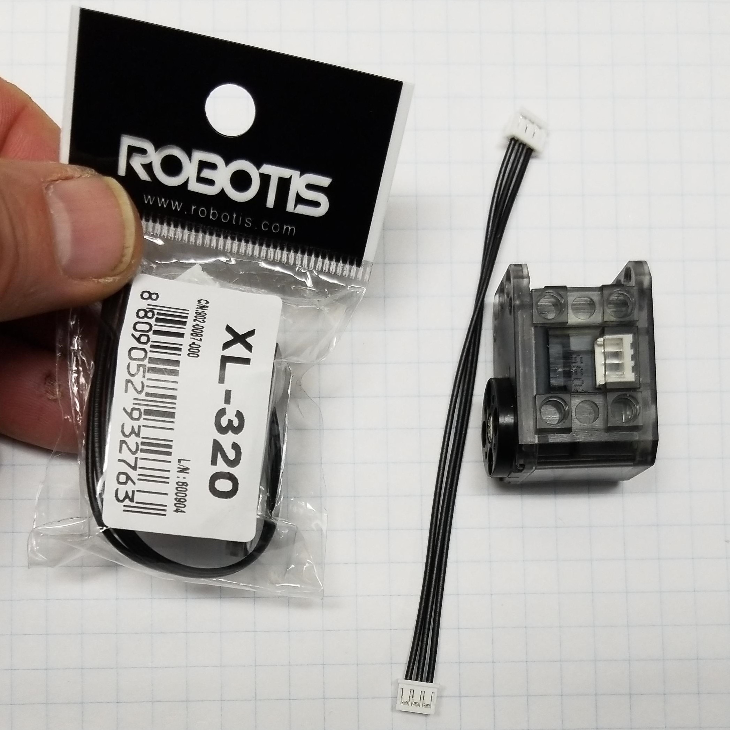
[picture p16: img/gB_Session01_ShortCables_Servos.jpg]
2 short cables and servos


- Using the wire strippers/cutters, cut the plastic connector off of one of the short connection cables.
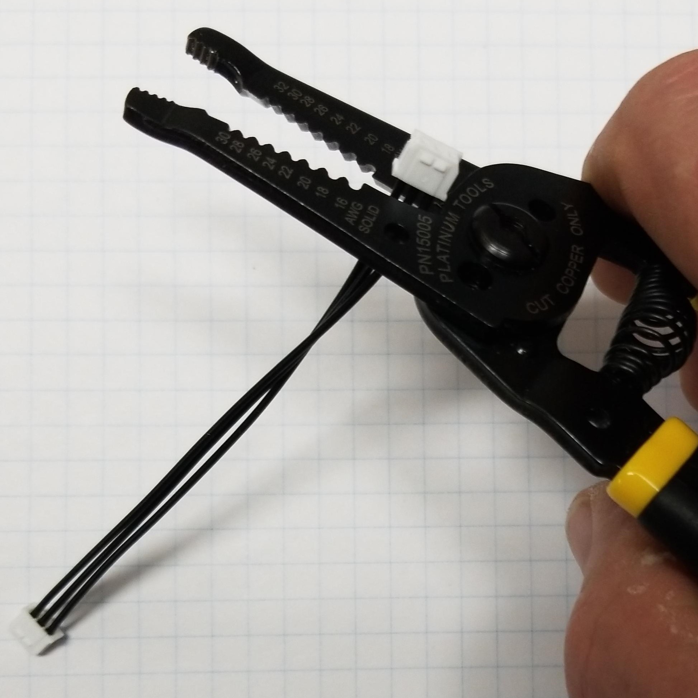
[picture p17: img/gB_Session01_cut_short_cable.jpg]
cut short cable connector


- Cut the Pin3 wire completely off the remaining connector and save it to use as a ground jumper wire.
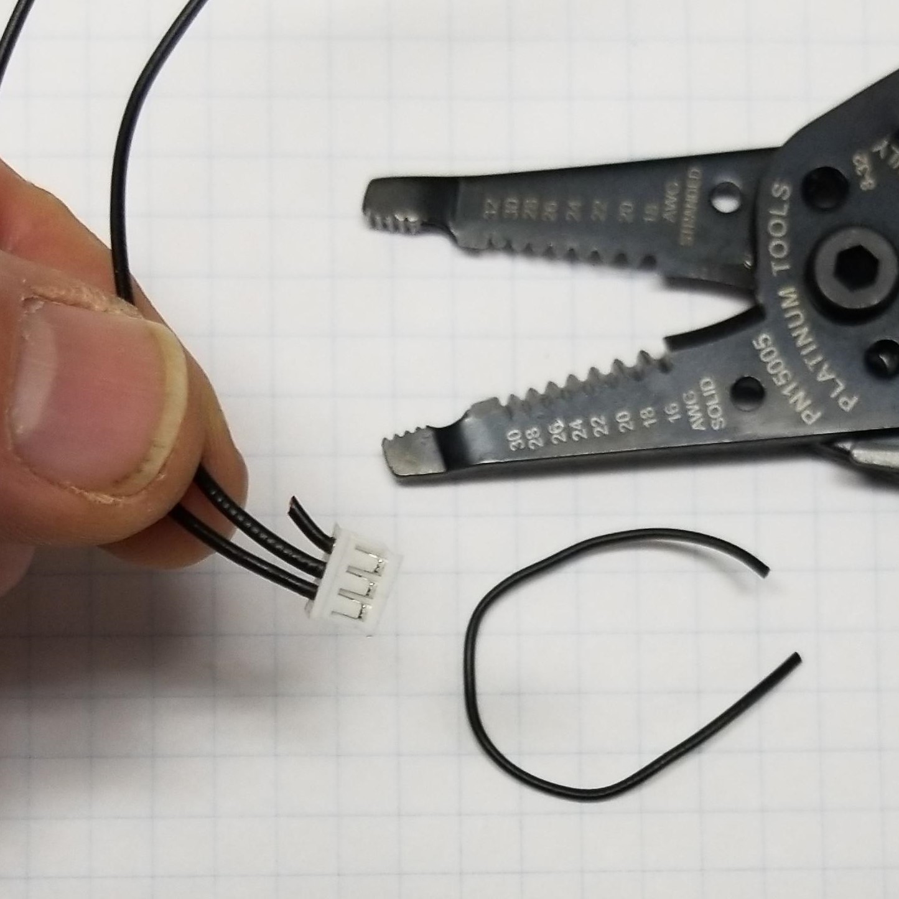
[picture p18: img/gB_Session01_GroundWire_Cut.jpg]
ground wire cutting

***Tip:*** Double check you are cutting the correct wire!
- Using the wire stripper's stranded 22-gauge slot, remove approximately 3mm of the insulation from each end of the ground jumper wire and the remaining two ends of the connector cable.
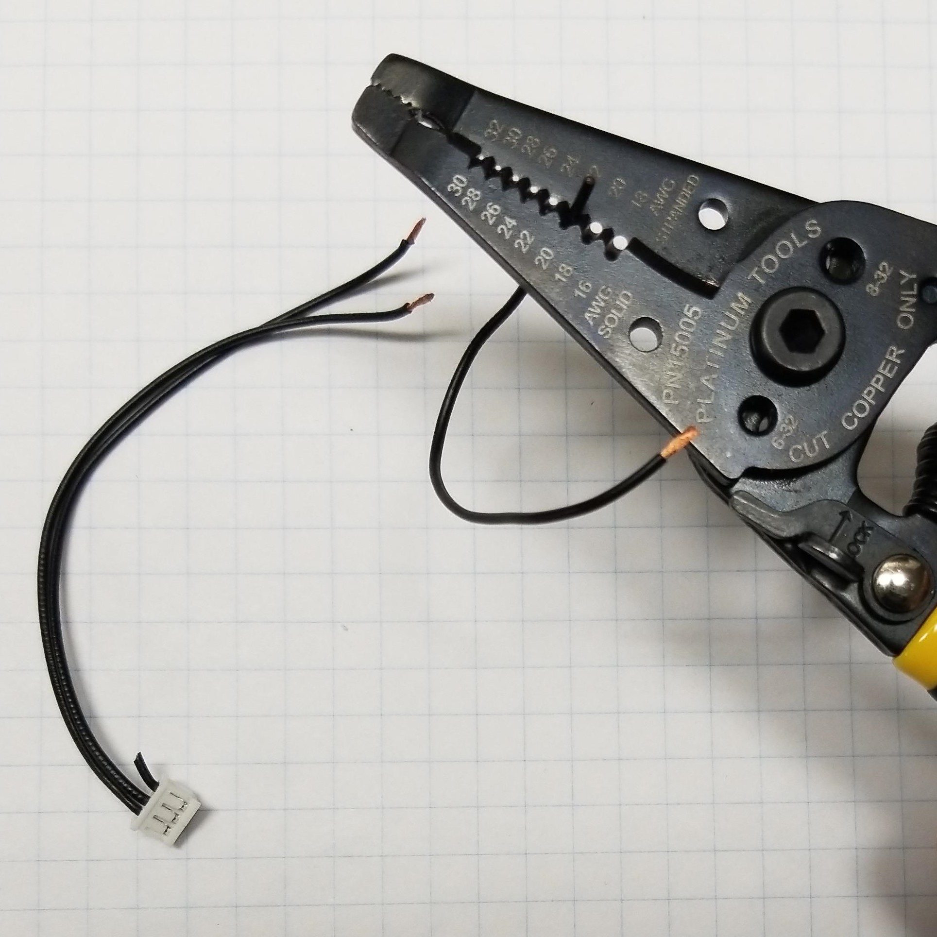
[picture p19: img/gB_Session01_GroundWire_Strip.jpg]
ground wire end stripping


- Using your fingers, twist the wire ends so that the strands hold together.
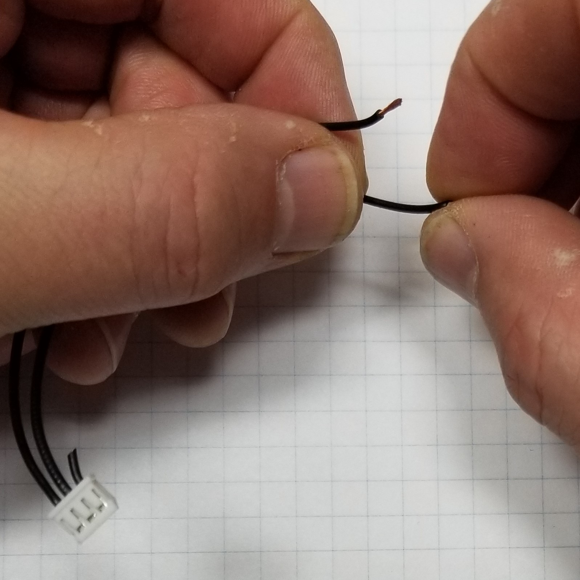
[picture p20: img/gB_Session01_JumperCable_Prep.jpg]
jumper cable preparation

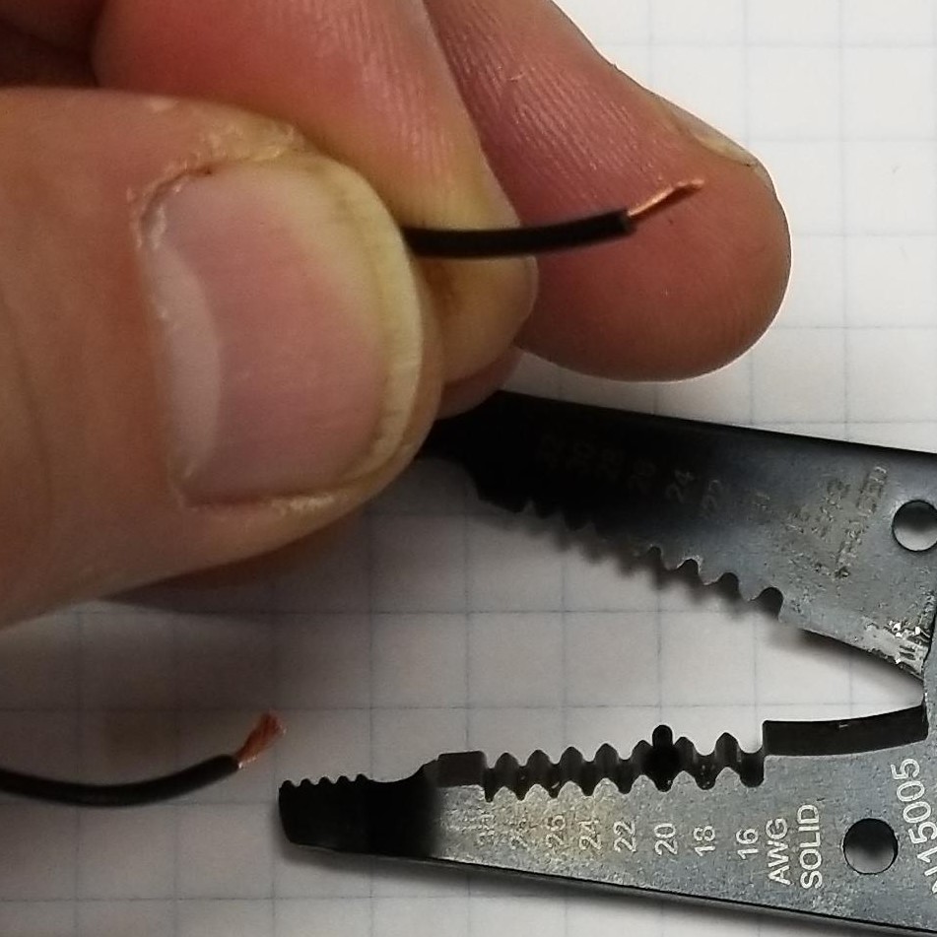
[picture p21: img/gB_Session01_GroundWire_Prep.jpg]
ground wire preparation


- Using the 2mm screwdriver, loosen the screw-clamps on the USB terminal block marked '**S**', '**-**', and '**+**'.
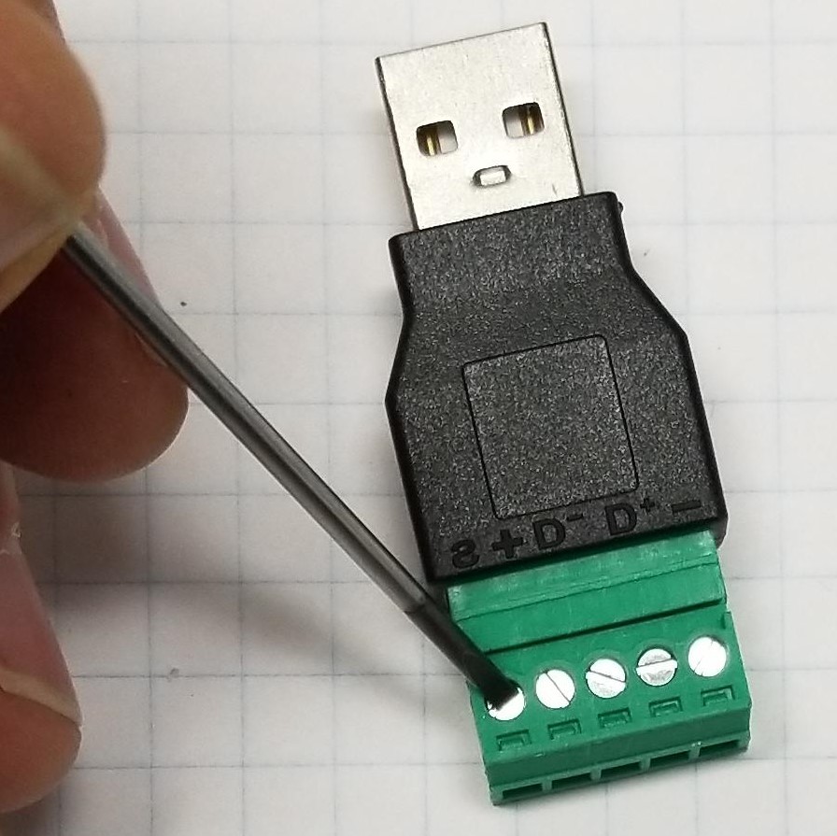
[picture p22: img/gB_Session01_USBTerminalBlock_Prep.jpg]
USB terminal block preparation

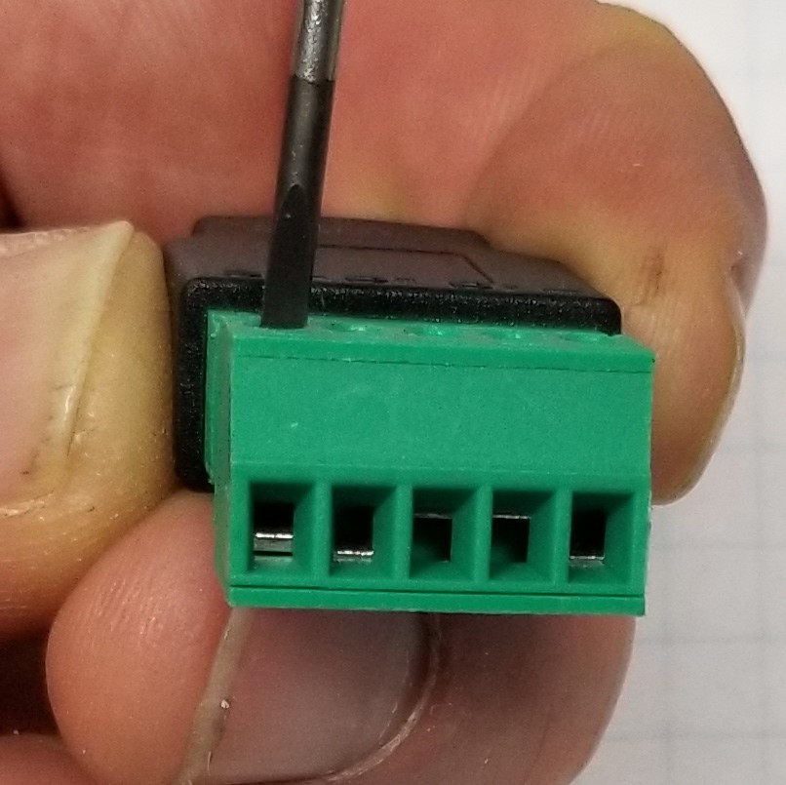
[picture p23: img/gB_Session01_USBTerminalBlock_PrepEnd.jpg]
USB terminal block preparation end view


- Insert one end of the prepared jumper wire into the USB terminal block's screw clamp marked "**-**" then tighten with the screw driver.
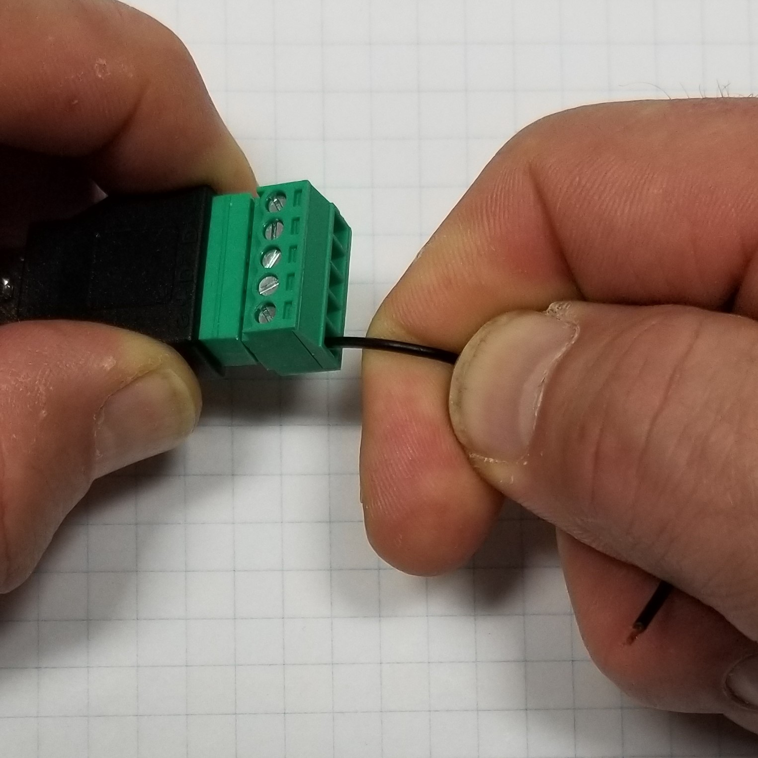
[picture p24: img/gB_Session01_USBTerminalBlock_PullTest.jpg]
USB terminal block pull-test

***Tip:*** Make sure the wire is correctly connected by firmly pulling on it and visually checking that it is not slipping out

- Connect the wires from the short cable to the USB Terminal Block:
  - Insert both the loose end of the prepared wire clamped into '**-**' and the cable wire connected to pin 1 into the wire clamp marked '**S**' then tighten with the screwdriver.

- Insert the cable wire connected to pin 2 on the connector into the wire clamp marked "**+**" (for positive voltage) and tighten with the screwdriver.
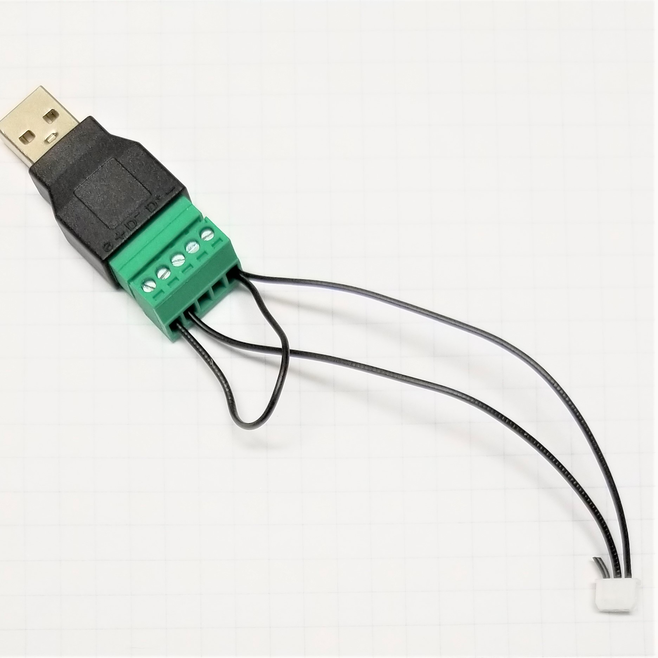
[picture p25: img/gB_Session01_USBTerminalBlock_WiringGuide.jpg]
USB terminal block wiring guide

***Tip:*** the jumper wire ties the negative side of the power provided by USB to chassis ground which reduces electromagnetic noise that may interfere with communications between the controller and the servos.

- Connect the USB Terminal Block to the Servo Controller with any one of the four three-pin connectors on the controller.
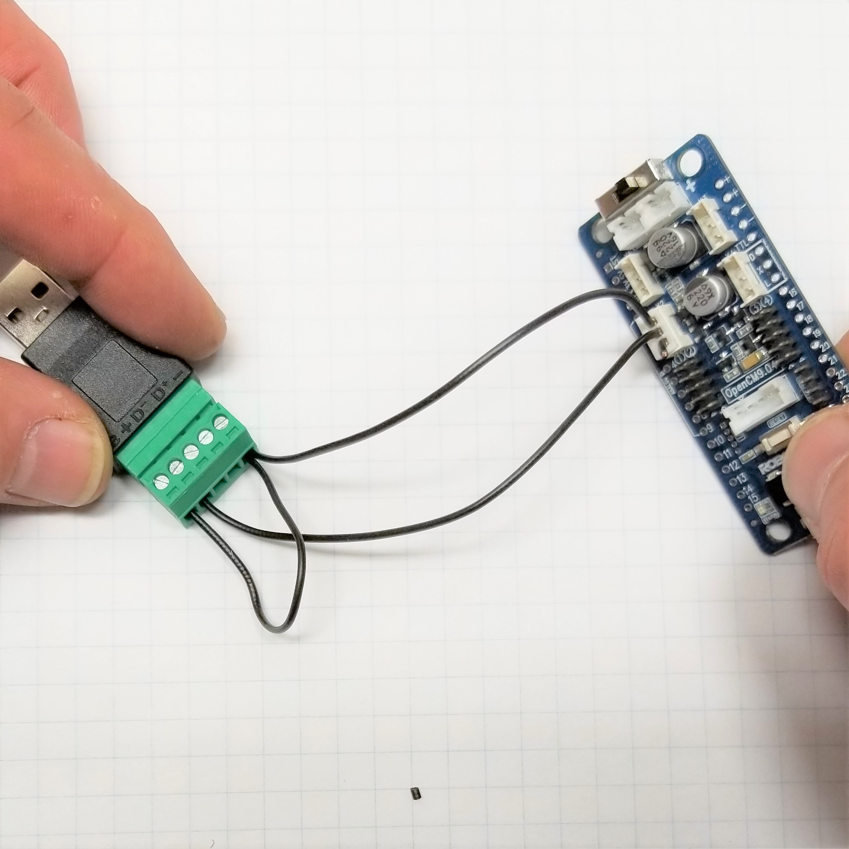
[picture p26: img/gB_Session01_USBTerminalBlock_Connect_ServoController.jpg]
connect servo controller to USB terminal block


- Plug the USB Terminal Block into the USB Hub using the port closest to the hub's link cable. Using the short USB-to-mini cable, connect the servo controller to any of the USB Hub's ports.
plug controller into USB hub

- Connect the servo to the servo controller with the remaining 130mm cable. The cable connector must snap into place on either connector on the servo. The other end of the cable can be inserted into any of the three remaining 3-pin connectors on the servo controller PC board. 
plug cable into servo
plug servo into controller
***Tip:*** Look closely at the cable connector ends and the receptacles to make sure the pin orientation is correct. If you push hard enough, it is possible to mistakenly insert them backwards. When inserted correctly, they will "snap" into place.

#### **Third, power it up!**

- Plug the USB Hub's power supply into an AC receptacle and insert its connector into the USB Hub. Observe a LED inside the servo flash red momentarily and a green LED on the controller turn on when power is applied.
observe servo red light flash

- Plug the USB Hub into your PC, then use Windows to open Device Manager and note which serial port number the servo controller is assigned to (for example: **"COM4"**)
gB_DeviceManager Com Port

## [**Next -> Session 2** - Communicate with the Servos](Session02.md)

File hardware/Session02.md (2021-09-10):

##  [Microsoft Applied Robotics Research Library](https://microsoft.github.io/AppliedRoboticsResearchLibrary/)
### Open Source Samples for Service Robotics
  
# [gestureBot Construction Guide](../hardware/README.md)

## **Session 2:** Configure the Servos

In this session we will 3D-print the robot's torso components while establishing the communication network for our servo motors by connecting them one-by-one to the PC and using a software tool to program each with a unique ID.
Servo ID Map

### Parts: 
- USB hub and power supply, servo, and servo controller assembly from Session 1
- servo set aside in Session 1
- (10) servos and their 130mm cables 

### Tools: 
- pen and light-colored tape for labeling servo ID's

Session 2 parts and tools
Session 2 servos

### **Procedure:**
#### **First, start 3D-printing the parts required for the next session:**
- [Hip Cover](https://github.com/microsoft/gestureBotDesignKit/blob/main/hardware/3D_print/gB_HipCover.stl)
- [Hip Swing Bracket](https://github.com/microsoft/gestureBotDesignKit/blob/main/hardware/3D_print/gB_SwingBracket_Hip.stl)
- [Servo Wheel](https://github.com/microsoft/gestureBotDesignKit/blob/main/hardware/3D_print/gBServoWheel.stl)
- [Upper Torso Frame](https://github.com/microsoft/gestureBotDesignKit/blob/main/hardware/3D_print/gB_UpperTorsoFrame.stl)
- [Servo Wheel](https://github.com/microsoft/gestureBotDesignKit/blob/main/hardware/3D_print/gb_SwingBracket_Hip.stl)
- [Servo Mount Plate](https://github.com/microsoft/gestureBotDesignKit/blob/main/hardware/3D_print/gb_UpperTorsoFrame.stl)

***Tip:*** Many 3D-printers have enough room on their build plate to print all of these models at the same time. Follow your printer's software instructions on how to add multiple models to a printing project file.

#### **Second, download and install the servo configuration software:**

- Download the Robotis Dynamixel Wizard 2.0 software appropriate for you platform from this web page:
http://en.robotis.com/service/downloadpage.php?ca_id=10

- Install and launch the Dynamixel Wizard 2.0 application, which provides a Graphical User Interface (GUI) for configuring the servo motors. If needed, installation instructions are provided on the this web page:
https://emanual.robotis.com/docs/en/software/dynamixel/dynamixel_wizard2/#introduction

- Select the **Options** button on the top level menu
- In the **Scan** section, adjust the following settings: 
  - select only Protocol 2.0
  - select the com port that showed up in Device Manager
  - select only 1000000 bps
  - leave the other options at default
  - select OK

  DynamixelWizard2 TopMenu Options

- Select the **Scan** button on the top level menu.
DynamixelWizard2 TopMenu ScanButton

- The scan should find one **XL-320** servo at **ID:001** in the list on the left side of the GUI,and show a list of the servo's memory page in the center of the GUI. Also, a device listed as **Unknown** at **ID:200** will appear in the list. This represents the servo controller PC board and can be ignored. In the left-side list, select the **[ID:001]XL-320** servo node.
DynamixelWizard2 TopMenu Select Servo ID:001

- In the memory page list, select and highlight row Address 3, which contains the servo's ID.  If the servo is brand new out-of-the-package, it should already be set to Decimal value "1".
DynamixelWizard2 TopMenu Select Servo ID Row 3

- When the Address row is selected, a window labeled ID will appear in the lower right corner of the application GUI. In the list of available addresses, select address 2 (Decimal) and then select "Save" below.
DynamixelWizard2 TopMenu Set Servo ID UI to 2

- The memory page list should now show the value Decimal 2 in the ID row.
DynamixelWizard2 TopMenu Servo Programmed ID2

- In the upper right corner of the UI basic controls for the XL-320 are available. By turning the **Torque** switch on and then selecting a position on the wheel, the servo horn will rotate to that position. Feel free to try out turning the LED off and on and switching from the **Joint** to **Wheel** mode. You will notice that other UI's appear on the right side of the application when different rows are selected in the memory page. ***For now, don't change any other parameter other than the servo ID.***
DynamixelWizard2 TopMenu Servo ControlUI
***Tip:*** Be sure to return to **Joint** mode before you finish.

- Label the newly programmed servo as ID:2 with tape and a pen, or return the servo to the bag and label the bag, or whatever method works best for you to identify the servo ID later.
label the servo

#### **Third, program the servo ID's from 1 to 12:**

- Disconnect the labeled servo and repeat the process above until each of the servos has been programmed and labeled with a unique ID from 1 through 12.
programmed servos

***Tip:*** Removing the cable from the servo requires significant force, but the Robotis cables are strong and designed for this. Grip the cable between your thumb and the side of your index finger near the servo-side connector and grip the servo with your other hand. Without jerking, pull the cable firmly up and out of the connector.

disconnect servo cable

## [**Next -> Session 3**: Assemble the Torso](Session03.md)

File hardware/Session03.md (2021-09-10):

##  [Microsoft Applied Robotics Research Library](https://microsoft.github.io/AppliedRoboticsResearchLibrary/)
### Open Source Samples for Service Robotics
  
# [gestureBot Construction Guide](../hardware/README.md)

## **Session 3:** Assemble the Torso
In this session we will 3D-print the head components while assembling the gestureBot's torso.

### Parts: 
- (3) servos labeled ID:004, ID:003, and ID:002 programmed in Session 2
- (4) 130MM servo cables
- (22) short plastic rivets
- (5) long plastic rivets
- (4) 3mm miniature steel screws
- [Base Frame](https://github.com/microsoft/gestureBotDesignKit/blob/main/hardware/3D_Print/gB_BaseFrame.stl) 3D-printed in Session 1, the base frame is the lower torso component and provides the stationary mounting point for servo ID:004 and anchors all of the moving parts of the gestureBot.
- [Hip Cover](https://github.com/microsoft/gestureBotDesignKit/blob/main/hardware/3D_print/gb_HipCover.stl) 3D-printed in Session 2, the hip cover attaches to the base frame and it's spherical shape allows the gestureBot's hip joint to move without exposing its interior.
- [Hip Swing Bracket](https://github.com/microsoft/gestureBotDesignKit/blob/main/hardware/3D_print/gb_SwingBracket_Hip.stl) 3D-printed in Session 2, the hip swing bracket and servo wheel attach to servo ID:004 and ID:003 rotating vertically to allow the entire gestureBot to lean forward and backward.
- [Upper Torso Frame](https://github.com/microsoft/gestureBotDesignKit/blob/main/hardware/3D_print/gb_UpperTorsoFrame.stl) 3D-printed in Session 2, the upper torso frame and mount plate connect to servo ID:003 allowing the gestureBot's torso to rotate horizontally, as well as providing mount points for servo ID:002 which rotates the head horizontally and servos ID:005 and ID:009 which rotate the arm assemblies vertically.
- [Servo Wheel](https://github.com/microsoft/gestureBotDesignKit/blob/main/hardware/3D_print/gb_SwingBracket_Hip.stl) 3D-printed in Session 2, the servo wheel supports servo ID:004 in the hip swing bracket.
- [Servo Mount Plate](https://github.com/microsoft/gestureBotDesignKit/blob/main/hardware/3D_print/gb_UpperTorsoFrame.stl) 3D-printed in Session 2, the servo mount plate supports servo ID:002 in the upper torso frame.

### Tools: 
- PH0 Phillips screwdriver
- plastic rivet tool

Session 3 parts and tools

### **Procedure:**
#### **First, start 3D-printing the parts required for the next session:**
- [Neck](https://github.com/microsoft/gestureBotDesignKit/blob/main/hardware/3D_print/gb_Neck.stl) 3D-printed in Session 3
- [Head Swing Bracket](https://github.com/microsoft/gestureBotDesignKit/blob/main/hardware/3D_print/gb_SwingBracket_Head.stl) 3D-printed in Session 3
- [Servo Wheel](https://github.com/microsoft/gestureBotDesignKit/blob/main/hardware/3D_print/gb_ServoWheel.stl) 3D-printed in Session 3
- [Head Frame](https://github.com/microsoft/gestureBotDesignKit/blob/main/hardware/3D_print/gb_HeadFrame.stl) 3D-printed in Session 3
- [Face](https://github.com/microsoft/gestureBotDesignKit/blob/main/hardware/3D_print/gb_Face.stl) 3D-printed in Session 3
- [Speaker](https://github.com/microsoft/gestureBotDesignKit/blob/main/hardware/3D_print/gb_Speaker.stl) 3D-printed in Session 3

**Hint:** Many 3D-printers have enough room on their build plate to print all of these models at the same time. Follow your printer's software instructions on how to add multiple models to a printing project file.

#### **Second, learn how to ensure the gripping performance of plastic rivets:**
It is easy to install plastic rivets incorrectly and decrease their grip and fastening strength. To work well, care must be taken not to deform their shape or crush their structure when inserting them into their mount holes. 

Damaged rivets versus functional rivets

Generally, the plastic covers of the servo motors are molded (not 3D-printed) from high-quality plastic. Their precision shapes are stable and do not present a problem for plastic rivets. However, parts printed by desktop 3D-printers may have shape variances that may negatively impact the way the rivets work.  Issues such as printer settings, calibration drift, quality and type of the plastic filament supply, print head wear, and environmental conditions such as temperature, humidity or vibrations can all affect the strength, flexibility, and shape precision of the parts they print.

tool small hole crushing rivet

To prevent these factors from impacting rivet strength, make sure that the mount holes are a full 3mm in diameter. If they are too small they will crush and deform the rivet shell, preventing their tips from expanding when the pin is inserted and gripping the inside edge of the mount hole. If this is the case with the mount holes in your 3D-printed parts, be sure to enlarge them with a 3mm drill bit, a rotary deburring tool, or a needle file.

expanding rivet hole

When inserting a rivet, the shell must reach far enough into the material layers it is fastening that the ridges on its end extend past the edge of the last layer. Ideally, the ridge edge and the material edge match perfectly. When the pin is inserted, the shell expands and pushes the ridge edges over the material edge and should produce a satisfying "snap" feeling. This action creates a gripping shelf that prevents the rivet from exiting the hole. If the rivet does not fully expand, only the friction pressure of the rivet shell against the side of the hole will hold it in, which is a much weaker form of fastening and generally will work loose as the robot moves during normal operation. 

#### **Third, assemble the components of the torso:**

- Mount servo ID:003 to the hip bracket by installing 6 rivets.
mount servo to hip bracket with rivets
servo mounted to hip bracket

- Connect (2) 130mm cables to servo.
connect cables to servo

- Install servo wheel with a long rivet. Do not insert a pin into the long rivet, friction will be sufficient to hold the rivet through the 3 layers and the servo wheel must spin freely.
install servo wheel

- Install servo ID:004 into the hip bracket, making sure that the servo horn (wheel that moves) is at its 0-degree postion. Check that the small single tick-mark on the horn is aligned with the tick-mark on the servo housing, as well as the tick-mark on the swing bracket.
check alignment of servo horn and bracket

- Fasten servo ID:004 to the bracket with (4) screws.
install servo with screws

- Connect servo ID003 to servo ID004 with one of its 130mm cables.
connect servo cables

- Connect 130mm cable to servo ID004.
connect servo cables

- Mount servo ID:004 to base frame with (6) rivets, routing cable through side gap between mount holes.
mount servo to base frame
mount servo to base frame interior

- Route servo ID:004 cable through access hole in base frame.
route servo cable through base frame

- Install the hip cover over servos ID:003 and ID:004 and onto the base frame. While not functionally significant, it might be aesthetically preferrable to align the ridges of the hip cover with the ridges on the base frame.
install hip cover
align hip cover

- Mount upper torso frame to servo ID003 with (4) short rivets, taking care servo horn tick-mark is aligned with tick-mark on servo housing.
mount upper torso frame to servo
mount upper torso frame to servo

- Attach servo ID:002 mount plate with (4) short rivets.
mount servo mount plate
install mount plate rivets

- Connect servo ID:003 to servo ID:002 with 130mm cable
connect servo cables

- Mount servo ID:002 to upper torso frame with mount plate, taking care to route 130mm cables through gaps between mounting holes at bottom of servo.
mount servo to upper torso frame

- Use (2) long rivets in the bottom mount plate holes.
mount servo to upper torso frame with long rivets
- Use (4) short rivets in the back mount plate holes.
mount servo to upper torso frame with mount plate

- Inspect The completed upper torso assembly.
completed upper torso assembly

## [**Next -> Session 4:** Assemble the Head Structure](Session04.md)

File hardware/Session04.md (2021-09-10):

##  [Microsoft Applied Robotics Research Library](https://microsoft.github.io/AppliedRoboticsResearchLibrary/)
### Open Source Samples for Service Robotics
  
# [gestureBot Construction Guide](../hardware/README.md)

## **Session 4:** Assemble the Head Structure
In this session we will 3D-print the components for both arms while assembling the structural components of the gestureBot's head.

### Parts: 
- servo labeled ID:001 programmed in Session 2
- 130MM servo cable
- (22) short plastic rivets
- (5) long plastic rivets
- (8) 3mm miniature steel screws
- [Neck](https://github.com/microsoft/gestureBotDesignKit/blob/main/hardware/3D_print/gb_Neck.stl) 3D-printed in Session 3, the neck is connected to servo ID:002 that rotates horizontally allowing the gestureBot to turn its head and servo ID:001.
- [Head Swing Bracket](https://github.com/microsoft/gestureBotDesignKit/blob/main/hardware/3D_print/gb_SwingBracket_Head.stl) 3D-printed in Session 3, the head swing bracket and servo wheel are attached to servo ID:001 that rotates vertically allowing the gestureBot to look up and down.
- [Servo Wheel](https://github.com/microsoft/gestureBotDesignKit/blob/main/hardware/3D_print/gb_ServoWheel.stl) 3D-printed in Session 3, the servo wheel supports servo ID:001 in the head swing bracket.
- [Head Frame](https://github.com/microsoft/gestureBotDesignKit/blob/main/hardware/3D_print/gb_HeadFrame.stl) 3D-printed in Session 3, the head frame attaches to the head swing bracket and provides a mount point for the speaker and face components.
- [Face](https://github.com/microsoft/gestureBotDesignKit/blob/main/hardware/3D_print/gb_Face.stl) 3D-printed in Session 3, the face connects to the head frame and provides a mount point for the speaker and the eyes.
- [Speaker](https://github.com/microsoft/gestureBotDesignKit/blob/main/hardware/3D_print/gb_Speaker.stl) 3D-printed in Session 3, the speaker is a mounting component intended as a placeholder for a speakspeaker modification in the future.

### Tools: 
- PH0 Phillips screwdriver
- plastic rivet tool

Session04 parts and tools

### **Procedure:**

#### **First, start 3D-printing the parts required for both arm assemblies:**
- [(4) Screw Mount Swing Bracket](https://github.com/microsoft/gestureBotDesignKit/blob/main/hardware/3D_print/gb_SwingBracket.stl)
- [(4) Servo Wheel](https://github.com/microsoft/gestureBotDesignKit/blob/main/hardware/3D_print/gb_ServoWheel.stl)
- [(6) Servo Mount Plate](https://github.com/microsoft/gestureBotDesignKit/blob/main/hardware/3D_print/gb_ServoMountPlate.stl)

#### **Second, assemble the head structure:**
- Mount the neck to the horn () of servo ID:002, taking care to align the tick-marks of the servo cover, the horn, and the neck component.
mount neck

- Route the 130mm cable from servo ID:002 through the holes in the neck.
route neck cable

- Connect the 130mm cable to servo ID:001.
connect neck cable

- Mount servo ID:001 to neck with (4) rivets.
mount head servo

- Mount the speaker component and head frame to face with (4) M1 10mm machine screws.
mount speaker to headframe
mount headframe to face

- Attach servo wheel to head swing bracket with long rivet. Do not install the rivet pin to allow the servo wheel to rotate freely.
install headbracket servo wheel

- Install servo ID:001 to head swing bracket taking care to align servo horn tick-mark with tick-mark on bracket.
install headbracket servo screws

- Mount face frame to head swing bracket with (4) long rivets. Installing the rivet pins is not recommended to accomodate future modifications and disassembly.
mount face frame to head swing bracket

- Inspect the gestureBot torso and head structure assemblies.
torso and head structures completed

## [**Next-> Session 5:** Assemble the Right Arm](Session05.md)

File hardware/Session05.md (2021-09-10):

##  [Microsoft Applied Robotics Research Library](https://microsoft.github.io/AppliedRoboticsResearchLibrary/)
### Open Source Samples for Service Robotics
  
# [gestureBot Construction Guide](../hardware/README.md)

## **Session 5:** Assemble the Right Arm
In this session we will 3D-print the base component while assembling the gestureBot's right arm.

### Parts: 
- servo labeled ID:005 programmed in Session 2
- (3) 130MM servo cable
- (16) short plastic rivets
- (2) long plastic rivets
- (16) 3mm miniature steel screws
- [(2) Screw Mount Swing Bracket](https://github.com/microsoft/gestureBotDesignKit/blob/main/hardware/3D_print/gb_SwingBracket.stl) 3D-printed in Session 4, the swing brackets and servo wheels form a shoulder joint between servos ID:005 and ID:006 and an elbow joint between servos ID:007 and ID:008.
- [(2) Servo Wheel](https://github.com/microsoft/gestureBotDesignKit/blob/main/hardware/3D_print/gb_ServoWheel.stl) 3D-printed in Session 4, the servo wheels support the swing bracket mounts for servo ID:006 and ID:008.
- [(2) Servo Mount Plate](https://github.com/microsoft/gestureBotDesignKit/blob/main/hardware/3D_print/gb_ServoMountPlate.stl) 3D-printed in Session 4, the servo mount plates support the servo ID:005 attachment to the upper torso frame and form a lower arm section between servo ID:006 and ID:007.

### Tools: 
- PH0 Phillips screwdriver
- plastic rivet tool

Session05 parts and tools

### **Procedure:**

#### **First, start 3D-printing the parts required for future sessions:**
- [Base](https://github.com/microsoft/gestureBotDesignKit/blob/main/hardware/3D_print/gb_Base.stl)

#### **Second, assemble the right arm:**
- Mount a swing bracket to servo ID:005 with (4) 3mm miniature screws, taking care to align the tick-marks on the servo horn, the servo cover, and the swing bracket.
mount right shoulder swing bracket

- Attach servo wheel to right shoulder swing bracket by inserting a long rivet through the bracket and into the back of servo ID:006. Do not install the rivet pin to allow the servo wheel to rotate freely.
mount right shoulder servo wheel

- Mount the servo ID:006 horn to the right shoulder swing bracket with (4) 3mm miniature screws and taking care to align servo horn ***double tick-marks*** with the tick-mark on the bracket. Note that in this case the alignment is made with the opposite side of the servo horn.
mount right shoulder swing bracket with screws

- With (3) short rivets, attach a servo mount plate to the back of servo ID:007 with the mount hole rings oriented length-wise to the servo.
attach servo7 mount plate

- Connect a 130mm cable to the top-side connector of servo ID:006. 
connect cable to top of servo6

- Attach servo ID:006 to ID:007 using (4) short rivets in the mount plate while routing the cable connected to servo ID:006 through the space between the servo and the mount plate.
attach servo6 to servo7 and route cable through mount plate

- Connect cable from servo ID:006 to servo ID:007 on its bottom-side connector.
connect cable to bottom of servo7

- Mount the right elbow swing bracket to servo ID:007 with (4) 3mm miniature screws taking care to align the tick-mark on the servo horn with the tick-mark on the servo cover and the bracket.
attach swing bracket to servo7

- Attach servo wheel to right elbow swing bracket by inserting a long rivet through the bracket and into the back of servo ID:008. Do not install the rivet pin to allow the servo wheel to rotate freely.
mount right shoulder servo wheel

- Mount the servo ID:008 horn to the right elbow swing bracket with (4) 3mm miniature screws and taking care to align servo horn ***double tick-marks*** with the tick-mark on the bracket. Note that in this case the alignment is made with the opposite side of the servo horn.
mount right elbow swing backet with screws

- Connect a 130mm cable from the top connector of servo ID:007 to the rear-side connector of servo ID:008.
connect servo7 to servo8

- Connect a 130mm cable from the rear-side connector of servo ID:005 to the bottom-side connector of servo ID:006.
connect servo7 to servo8

## [**Next-> Session 6:** Assemble the Left Arm](Session06.md)

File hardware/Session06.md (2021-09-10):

##  [Microsoft Applied Robotics Research Library](https://microsoft.github.io/AppliedRoboticsResearchLibrary/)
### Open Source Samples for Service Robotics
  
# [gestureBot Construction Guide](../hardware/README.md)

## **Session 6:** Assemble the Left Arm
In this session we will 3D-print the eye and ear components (in an alternate color if desired) while assembling the gestureBot's left arm.

### Parts: 
- servos labeled ID:009, ID:010, ID:011, and ID:012 programmed in Session 2
- (3) 130MM servo cable
- (16) short plastic rivets
- (2) long plastic rivets
- (16) 3mm miniature steel screws
- [(2) Screw Mount Swing Bracket](https://github.com/microsoft/gestureBotDesignKit/blob/main/hardware/3D_print/gb_SwingBracket.stl) 3D-printed in Session 4, the swing brackets and servo wheels form a shoulder joint between servos ID:009 and ID:010 and an elbow joint between servos ID:011 and ID:012.
- [(2) Servo Wheel](https://github.com/microsoft/gestureBotDesignKit/blob/main/hardware/3D_print/gb_ServoWheel.stl) 3D-printed in Session 4, the servo wheels support the swing bracket mounts for servo ID:010 and ID:012.
- [(2) Servo Mount Plate](https://github.com/microsoft/gestureBotDesignKit/blob/main/hardware/3D_print/gb_ServoMountPlate.stl) 3D-printed in Session 4, the servo mount plates support the servo ID:009 attachment to the upper torso frame and form a lower arm section between servo ID:010 and ID:011.

### Tools: 
- PH0 Phillips screwdriver
- plastic rivet tool

Session06 parts and tools

### **Procedure:**

#### **First, start 3D-printing the parts required for future sessions:**
- [Eyes (use alternative color plastic if desired)](https://github.com/microsoft/gestureBotDesignKit/blob/main/hardware/3D_print/gb_Eyes.stl)
- [(2) Ear (use alternative color plastic if desired)](https://github.com/microsoft/gestureBotDesignKit/blob/main/hardware/3D_print/gb_Ear.stl)

#### **Second, assemble the left arm:**
- Mount a swing bracket to servo ID:009 with (4) 3mm miniature screws, taking care to align the tick-marks on the servo horn, the servo cover, and the swing bracket.
mount left shoulder swing bracket

- Attach servo wheel to left shoulder swing bracket by inserting a long rivet through the bracket and into the back of servo ID:010. Do not install the rivet pin to allow the servo wheel to rotate freely.
mount left shoulder servo wheel

- Mount the servo ID:010 horn to the left shoulder swing bracket with (4) 3mm miniature screws and taking care to align servo horn ***double tick-marks*** with the tick-mark on the bracket. Note that in this case the alignment is made with the opposite side of the servo horn.
mount left shoulder swing bracket with screws

- With (3) short rivets, attach a servo mount plate to the back of servo ID:011 with the mount hole rings oriented length-wise to the servo.
attach Servo11 mount plate

- Connect a 130mm cable to the top-side connector of servo ID:010. 
connect cable to top of servo10

- Attach servo ID:010 to ID:011 using (4) short rivets in the mount plate while routing the cable connected to servo ID:010 through the space between the servo and the mount plate.
attach servo6 to Servo11 and route cable through mount plate

- Connect cable from servo ID:010 to servo ID:011 on its bottom-side connector.
connect cable to bottom of Servo11

- Mount the left elbow swing bracket to servo ID:011 with (4) 3mm miniature screws taking care to align the tick-mark on the servo horn with the tick-mark on the servo cover and the bracket.
attach swing bracket to Servo11

- Attach servo wheel to left elbow swing bracket by inserting a long rivet through the bracket and into the back of servo ID:012. Do not install the rivet pin to allow the servo wheel to rotate freely.
mount left shoulder servo wheel

- Mount the servo ID:012 horn to the left elbow swing bracket with (4) 3mm miniature screws and taking care to align servo horn ***double tick-marks*** with the tick-mark on the bracket. Note that in this case the alignment is made with the opposite side of the servo horn.
mount left elbow swing backet with screws

- Connect a 130mm cable from the top connector of servo ID:011 to the rear-side connector of servo ID:012.
connect Servo11 to Servo12

- Connect a 130mm cable from the rear-side connector of servo ID:009 to the bottom-side connector of servo ID:010.
connect Servo11 to Servo12

## [**Next-> Session 7:** Attach the Arms and Test the Servos](Session07.md)

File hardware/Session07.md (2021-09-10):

##  [Microsoft Applied Robotics Research Library](https://microsoft.github.io/AppliedRoboticsResearchLibrary/)
### Open Source Samples for Service Robotics
  
# [gestureBot Construction Guide](../hardware/README.md)

## **Session 7:** Attach the Arms and Test the Servos
In this session we will 3D-print the hood component (in an alternate color if desired) while we attach the arms to the torso and test the servos using the Robotis Dynamixel Wizard 2.0 application.

### Parts: 
- controller electronics assembly completed in [Session 1](Session01.md)
- head and torso completed in [Session 4](Session04.md)
- right arm assembly completed in [Session 5](Session05.md)
- left arm assembly completed in  [Session 6](Session06.md)
- (2) 190MM servo cables
- (24) short plastic rivets
- [(2) Servo Mount Plate](https://github.com/microsoft/gestureBotDesignKit/blob/main/hardware/3D_print/gb_ServoMountPlate.stl) 3D-printed in Session 4, the servo mount plates support servos' ID:005 and ID:009 (from the arm assemblies) attachment to the upper torso frame.
- [Base](https://github.com/microsoft/gestureBotDesignKit/blob/main/hardware/3D_print/gb_Base.stl) 3D-printed in Session 4, the base supports the entire gestureBot. The tabs on the bottom of the base frame insert into the base to provide a stable platform as well as space to contain the controller electronics and USB3 hub.

### Tools: 
- plastic rivet tool

Session07 parts and tools
USB3 Hub terminal block and servo controller

### **Procedure:**

#### **First, start 3D-printing the parts required for future sessions:**
- [Hood (use alternative color plastic if desired)](https://github.com/microsoft/gestureBotDesignKit/blob/main/hardware/3D_print/gb_Hood.stl)

#### **Second, attach the arms to the torso:**
- Attach the mount plate to servo ID:005 in the **right** arm assembly using (4) short rivets.
attach mount plate servo5

- Attach the mount plate to servo ID:009 in the **left** arm assembly using (4) short rivets.
attach mount plate servo9

- Route the cable connecting servo ID:005 and ID:006 through the space between the bottom-rear rivet mount holes of servo ID:005.
route cable servo5

- Mount the right arm assembly to the upper torso frame using (8) short rivets.
attach right arm to upper torso

- Route the cable connecting servo ID:009 and ID:010 through the space between the bottom-rear rivet mount holes of servo ID:009.
route cable servo9

- Mount the left arm assembly to the upper torso frame using (8) short rivets.
attach left arm to upper torso

- Connect the (2) 190mm cables to the front-side connectors of servos ID:005 and ID:009.
connect long cables to servo5 and servo9

- Route the (2) 190mm cables connected to servos ID:005 and ID:009 along with the 130mm cable connected to servo ID:004 down through the hip cover and the square hole in the top of the base frame.
route long cables through hip cover
route long and short cables through base frame

- ***With the USB3 hub power cable unplugged,*** insert the cables connected to servo ID:004, ID:005, and ID:009 into the three open connectors on the servo controller PC board.
connect cables to controller

- Place the controller electronics and USB3 hub into the base, with the USB terminal block resting in the right-side slot.
place controller and USB hub in base

- Insert the large curved tabs on the bottom of the base frame into the slots on the base, with the open end of the base toward the rear.
insert base frame in base

- Plug the power connector into the USB3 Hub and observe all of the servos flash red LED's.
insert base frame in base

#### **Third, test the servos:**
- With the USB3 hub power cable connected, insert the USB3 cable into the PC.
- On the PC, launch the Dynamixel Wizard 2.0 application.
launch DMW2

- Select the **Scan** button on the top-level menu and allow the dialog box to complete its scan and close by itself.
DMW2 TopMenu ScanButton

- Observe all twelve of the servo ID's listed in the left-side panel.
DMW2 servo list

- Test control and movement of each servo by selecting them one-by-one in the left-side list, then using the upper-right-side servo UI to turn torque on, move the servo slightly (approximately plus or minus 5 degrees), and then turn torque back off.
DMW2 servo tests
***Tip: Be cautious when manually commanding the servos to move.*** The gestureBot assembly will physically limit the servos' rotation due to body part collisions. If a servo is driven into a collision, it may cause damage to the parts or the servo. As a protective feature, the servos may automatically shutdown in these cases and require a reset by unplugging the USB hub from the computer and then the power cable from the USB hub, waiting 15 seconds, then first plugging the hub power and then the USB connection to the PC back in. Also, ***do not change the servos from 'Joint' to 'Motor' mode.*** If driven in Motor mode the servos will wind their connection cables causing damage or automatic shutdown.

## [**Next-> Session 8:** Complete the Head](Session08.md)

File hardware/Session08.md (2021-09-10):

##  [Microsoft Applied Robotics Research Library](https://microsoft.github.io/AppliedRoboticsResearchLibrary/)
### Open Source Samples for Service Robotics
  
# [gestureBot Construction Guide](../hardware/README.md)

## **Session 8:** Complete the Head
In this session we will 3D-print the hands and arm servo covers while we assemble the the head components.

### Parts: 
- gestureBot (partially assembled through Session 7)
- (4) short plastic rivets
- [Hood](https://github.com/microsoft/gestureBotDesignKit/blob/main/hardware/3D_print/gb_Hood.stl) 3D-printed in Session 7, the hood provides a cosmetic cover for the head structure assembly.
- [Eyes](https://github.com/microsoft/gestureBotDesignKit/blob/main/hardware/3D_print/gb_Eyes.stl) 3D-printed in Session 6, the eyes provide a cosmetic cover addition to the face component.
- [Ear](https://github.com/microsoft/gestureBotDesignKit/blob/main/hardware/3D_print/gb_Ear.stl) 3D-printed in Session 6, the ears provide cosmetic covers and removable access to the interior of the head assembly without requiring the hood to be removed.

### Tools: 
- PH0 Phillips screwdriver
- needle nose pliers

Session08 parts and tools

### **Procedure:**

#### **First, start 3D-printing the parts required for future sessions:**
- [(6) Servo Cover](https://github.com/microsoft/gestureBotDesignKit/blob/main/hardware/3D_print/gb_ServoCover.stl)
- [(12) Servo Side Cover](https://github.com/microsoft/gestureBotDesignKit/blob/main/hardware/3D_print/gb_ServoSideCover.stl)
- [(2) Hand](https://github.com/microsoft/gestureBotDesignKit/blob/main/hardware/3D_print/gb_Hand.stl)

#### **Second, attach the eyes, hood, and ears:**
- Mount the eyes component by inserting the two posts behind the face into the two holes in the bridge between the eyes.
mount eyes
***Tip:*** To avoid breaking the face component, be careful to support the face as you push the eyes onto the posts.
support face

- Mount the hood by tilting the head assembly forward, sliding the hood onto the head swing bracket and attaching the hood to the bracket with (4) rivets.
mount hood
***Tip:*** Using a pair of needle-nose pliers may be helpful in inserting the rivets.

- Attach the ears buy snapping each into the holes on the sides of the hood.
attach ears

- Inspect the complete head assembly.
complete head assembly

## [**Next-> Session 9:** Install the Body Covers](Session09.md)

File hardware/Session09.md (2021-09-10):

##  [Microsoft Applied Robotics Research Library](https://microsoft.github.io/AppliedRoboticsResearchLibrary/)
### Open Source Samples for Service Robotics
  
# [gestureBot Construction Guide](../hardware/README.md)

## **Session 9:** Install the Body Covers
In this session we will 3D-print the torso cover components while we attach the hands and the arm servo covers. All of the cover components are designed to be removable without disassembling the gestureBot. At this point the gestureBot is ready to run the Labanotation Suite software applications. The torso covers can be attached as soon as they are finished printing.

### Parts: 
- [(6) Servo Covers](https://github.com/microsoft/gestureBotDesignKit/blob/main/hardware/3D_print/gb_ServoCover.stl)
- [(8) Servo Side Covers](https://github.com/microsoft/gestureBotDesignKit/blob/main/hardware/3D_print/gb_ServoSideCover.stl)
- [(4) Screw-side Swing Bracket Covers](https://github.com/microsoft/gestureBotDesignKit/blob/main/hardware/3D_print/gB_BracketCover_ScrewSide.stl)
- [(4) Rivet-side Swing Bracket Covers](https://github.com/microsoft/gestureBotDesignKit/blob/main/hardware/3D_print/gB_BracketCover_RivetSide.stl)
- [(2) Hand](https://github.com/microsoft/gestureBotDesignKit/blob/main/hardware/3D_print/gb_Hand.stl)
- [Upper Torso Front Cover](https://github.com/microsoft/gestureBotDesignKit/blob/main/hardware/3D_print/gb_UpperTorsoFrontCover.stl)
- [Upper Torse Back Cover](https://github.com/microsoft/gestureBotDesignKit/blob/main/hardware/3D_print/gB_UpperTorsoBackCover.stl)

Session09 parts and tools

### **Procedure:**

#### **First, start 3D-printing the parts required for future sessions:**
- [Upper Torso Front Cover](https://github.com/microsoft/gestureBotDesignKit/blob/main/hardware/3D_print/gb_UpperTorsoFrontCover.stl)
- [Upper Torse Back Cover](https://github.com/microsoft/gestureBotDesignKit/blob/main/hardware/3D_print/gB_UpperTorsoBackCover.stl)

#### **Second, install the right arm covers and hands:**
- Route the cable connecting servo ID:006 to ID:005 folding downward and between the side servo mounting holes, then slide the cover over the servo.
Install servo 6 cover 

- Install the servo ID:006 top-side cover by sliding it over the servo cover's ridges.
Install servo 6 top side cover 

- Install the servo ID:006 bottom-side cover by sliding it over the servo cover's ridges and routing the connection cable between the side cover and the servo wheel.
Install servo 6 bottom side cover 
***Tip:*** The bottom side cover may need to be slightly cut down if it interferes with the swing bracket.

- Route the cable connecting servo ID:006 and ID:007 folding downward and between the bottom servo mounting holes, then slide the cover over the servo.
Install servo7 cover 

- Install the servo ID:007 top-side cover by sliding or snapping it over the servo cover's ridges.
Install servo7 top-side cover 

- Install the servo ID:007 bottom-side cover by sliding or snapping it over the servo cover's ridges and routing the cable connecting servo ID:007 to ID:008 through the gap between the servo mounting holes.
Install servo7 bottom-side cover 

- Route the cable connecting servo ID:007 to ID:008 folding to downward across the connector and between the side servo mounting holes, then slide the cover over the servo.
Install servo 8 cover 

- Install the servo ID:008 hand by sliding over the servo cover's side ridges.
Install servo 8 hand 

- Install the servo ID:006 rivet-side swing bracket cover by inserting its post into the long rivet hole.
Install servo 6 bracket cover rivet side 

- Install the servo ID:008 rivet-side swing bracket cover by inserting its post into the long rivet hole.
Install servo 8 bracket cover rivet side 

- Install the servo ID:006 screw-side swing bracket cover by inserting its post into the bracket hole.
Install servo 6 bracket cover screw side 

- Install the servo ID:008 rivet-side swing bracket cover by inserting its post into the bracket hole.
Install servo 8 bracket cover screw side 

#### **Third, repeat the procedure above installing the servo covers and hands for the left arm:**

Install left arm covers and hand

#### **Fourth, install the upper torso covers:**
- Slide the upper torso cover over the gestureBot from front to back and taking care to route the cable connecting the shoulder and upper arm servos through the slot on the side of the cover.
Install upper torso front cover

- Install the upper torso back cover by hooking it over the side ridges on the front cover, taking care to place the offset tab on the cover's "wings" on the inside of the front cover, and then snapping it into place.
Install upper torso back cover

- Inspect the completed gestureBot covers.
complete covers

## [**Next-> Session 10:** Run the Gesture Applications](Session10.md)

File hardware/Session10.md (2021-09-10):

##  [Microsoft Applied Robotics Research Library](https://microsoft.github.io/AppliedRoboticsResearchLibrary/)
### Open Source Samples for Service Robotics
  
# [gestureBot Construction Guide](../hardware/README.md)

## **Session 10:** Run the Labanotation Gesture Applications
At this point the gestureBot hardware is complete and ready to run the Labanotation Suite software applications. 

### Parts: 
- Completed gestureBot
- Windows 10 PC with USB3 port

Session10 parts and tools

### **Procedure:**

#### **First, prep the PC to run applications with Python3.7:**
- Follow the software installation instructions for either the [Gesture Service](/src/Samples/gestureService_w2v/README.md) or (if you are in a hurry) [gestureBot](/src/Samples/gestureBot/README.md) sample projects included in this repository and verify that the browser-based user-interface (UI) services run successfully on the Windows 10 PC.
- Plug in the gestureBot's USB3 hub's power supply.
- Connect the gestureBot's USB cable to the PC.

#### **Second, run a script to set servo rotation limits:**
- To protect the gestureBot from being damaged with movement commands that cause collisions or pull cables, we will run the Python code in the sample folder: 

\gestureBotDesignKit\src\Samples\gestureBotSetLimits\

- Using Microsoft Visual Code or any text editor, open the file in the repository folder:
\gestureBotDesignKit\src\Samples\gestureBotSetLimits\main.py

- In **line 50**, change the value to match the serial port noted earlier for your gestureBot. For example:
```
    self.comPort = "com4"
```
***Tip:*** If needed, the serial port can be looked up in Windows Device Manager as shown at the end of [Session 1](Session01.md).

Following is an example run session:
```
C:\Users\robotics\github_repos\gestureBotDesignKit\src\Samples\gestureBotSetLimits>python main.py
gestureBot: connecting to port 'com4'...
ID: 1: setting CW angle limit to -70 (272)
ID: 1: setting CCW angle limit to 50 (682)
ID: 2: setting CW angle limit to -91 (201)
ID: 2: setting CCW angle limit to 91 (821)
gestureBot: disconnecting from port 'com4'...
```
***Tip:*** In the future, if you modify your gestureBot and want to set different safety limits, this code provides an example in the **run()** function starting at **line 270**.

#### **Third, run the Gesture Service sample application and connect it to the gestureBot:**

- Open the URL http://localhost:8001 in the browser.

gestureBot Controller UI

- In the Hardware section of the UI, enter the Port value for your gestureBot and select the Connect button.

- After connecting, the physical gestureBot will move to the current pose and thereafter track the on-screen virtual gestureBot movements until it is disconnected.

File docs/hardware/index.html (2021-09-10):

Microsoft Applied Robotics Research Library: gestureBotDesignKit

- Search
- Microsoft Applied Robotics Research Library
- Open Source Samples for Service Robotics
- gestureBot Construction Guide
- Before you begin...
- Safety Alert:
- Requirements
- Parts List
- Step-by-Step Instructions
- Session 1: Set Up the Servo Controller Electronics
- Session 2: Configure the Servos
- Session 3: Assemble the Torso
- Session 4: Assemble the Head Structure
- Session 5: Assemble the Right Arm
- Session 6: Assemble the Left Arm
- Session 7: Attach the Arms and Test the Servos
- Session 8: Complete the Head
- Session 9: Install the Body Covers
- Session 10: Run the Gesture Applications
- A last word...

##  Microsoft Applied Robotics Research Library (https://microsoft.github.io/AppliedRoboticsResearchLibrary/)

### Open Source Samples for Service Robotics

 (https://opensource.org/licenses/MIT)

# gestureBot Construction Guide

The gestureBot is adapted from the Mini (https://www.robotis.us/robotis-mini-intl/) robot kit from Robotis, Inc (https://www.robotis.us) and the MSRAbot project created by interns at Microsoft Research Asia. The information on this page will guide you through purchasing and printing parts, as well as step-by-step assembly of the gestureBot.

gestureBot wireframe

# Before you begin...

If you have experience in 3D printing and electronic assembly, we hope that you find this project relatively simple and straight-forward. Once the parts are in-hand, the time required to complete the project won't be much more than it takes to print the 3D models.

If you are not experienced in these areas, one of the first things you'll learn is that desktop 3D-printers are not a good source of instant gratification! Even the smallest of the models contained in this kit will take several hours to print, while some of the larger models take more than half a day. With those time requirements in mind, we broke the procedures down into work sessions that fit along with the 3D print operations. Alternatively, a class of 5-10 students taking on this project might be successful with serial use of a single 3D printer and meeting once-a-week to perform the other assembly tasks.

An important feature of these instructions is their sequence. Following the steps in the sessions in order is key to preventing the need to disassemble an assembly in order to have access to cable pathways or screw and rivet holes.

# Safety Alert:

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

## Requirements

Here are the physical things you'll need to build and use your gestureBot:

### PC

- x64 CPU
- Microsoft Windows 10
- USB3 port (USB2 can work in some cases)

### Tools

- 3D printer (we use an Ultimaker3 (https://ultimaker.com/3d-printers/ultimaker-3) with PLA filament)
- Wire Stripper/Cutter (https://vetco.net/products/16awg-32awg-wire-stripper-cutter/plat-15005c)
- small Phillips screwdriver (PH0) (https://vetco.net/products/general-tools-712010-precision-screwdriver-phillips-0)
- small flat-blade screwdriver (2mm) (https://vetco.net/products/)
- Alternative Screwdrivers:
  - 5 in 1 Precision Screwdriver (https://vetco.net/products/general-tools-spc606-jewelers-screwdriver-set-of-5)
  - 16 in 1 Precision Screwdriver (https://vetco.net/products/16-in-1-precision-screwdriver-set)
- pen and light-colored tape for labeling servo ID's

### Optional but Helpful Tools

- Rivet Tool (https://www.robotis.us/tool-stl/)
- needle-nose pliers
- Magnet (for easier screw driving) (https://vetco.net/products/3-4-round-magnet/son-pm550)
- 3mm drill bit, variable speed drill
- 3D-printing cleanup tools (https://www.matterhackers.com/articles/tools-of-the-trade-to-make-your-life-as-a-3d-print-master-much-simpler). A swivel deburring tool is especially useful.

## Parts List

### Purchased Parts

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

### 3D Printed Parts

ID | Qty | Name & Model Link | .
M1 | 1 | Base (https://github.com/microsoft/gestureBotDesignKit/blob/main/hardware/3D_Print/gB_Base.stl) | 
M2 | 1 | Base Frame (https://github.com/microsoft/gestureBotDesignKit/blob/main/hardware/3D_Print/gB_BaseFrame.stl) | 
M3 | 1 | Bracket Cover (Rivet Side) (https://github.com/microsoft/gestureBotDesignKit/blob/main/hardware/3D_Print/gB_BracketCover_RivetSide.stl) | 
M4 | 1 | Bracket Cover (Screw Side) (https://github.com/microsoft/gestureBotDesignKit/blob/main/hardware/3D_Print/gB_BracketCover_ScrewSide.stl) | 
M5 | 2 | Ear (https://github.com/microsoft/gestureBotDesignKit/blob/main/hardware/3D_Print/gB_Ear.STL) | 
M6 | 1 | Eyes (https://github.com/microsoft/gestureBotDesignKit/blob/main/hardware/3D_Print/gB_Eyes.STL) | 
M7 | 1 | Face (https://github.com/microsoft/gestureBotDesignKit/blob/main/hardware/3D_Print/gB_Face.STL) | 
M8 | 2 | Hand (https://github.com/microsoft/gestureBotDesignKit/blob/main/hardware/3D_Print/gB_Neck.stl) | 
M9 | 1 | Head Frame (https://github.com/microsoft/gestureBotDesignKit/blob/main/hardware/3D_Print/gB_HeadFrame.stl) | 
M10 | 1 | Hip Cover (https://github.com/microsoft/gestureBotDesignKit/blob/main/hardware/3D_Print/gB_HipCover.stl) | 
M11 | 1 | Hood (https://github.com/microsoft/gestureBotDesignKit/blob/main/hardware/3D_Print/gB_Hood.stl) | 
M12 | 1 | Neck (https://github.com/microsoft/gestureBotDesignKit/blob/main/hardware/3D_Print/gB_Neck.stl) | 
M13 | 1 | Servo Cover (https://github.com/microsoft/gestureBotDesignKit/blob/main/hardware/3D_Print/gB_ServoCover.stl) | 
M14 | 2 | Servo Mount Plate (https://github.com/microsoft/gestureBotDesignKit/blob/main/hardware/3D_Print/gB_ServoMountPlate.stl) | 
M15 | 2 | Servo Side Cover (https://github.com/microsoft/gestureBotDesignKit/blob/main/hardware/3D_Print/gB_ServoSideCover.stl) | 
M16 | 2 | Servo Wheel (https://github.com/microsoft/gestureBotDesignKit/blob/main/hardware/3D_Print/gB_ServoWheel.stl) | 
M17 | 2 | Speaker (https://github.com/microsoft/gestureBotDesignKit/blob/main/hardware/3D_Print/gB_Speaker.stl) | 
M18 | 2 | Head Swing Bracket (https://github.com/microsoft/gestureBotDesignKit/blob/main/hardware/3D_Print/gB_SwingBracket_Head.stl) | 
M19 | 2 | Hip Swing Bracket (https://github.com/microsoft/gestureBotDesignKit/blob/main/hardware/3D_Print/gB_SwingBracket_Hip.stl) | 
M20 | 1 | Screw-Mount Swing Bracket (https://github.com/microsoft/gestureBotDesignKit/blob/main/hardware/3D_Print/gB_SwingBracket_ScrewMount.stl) | 
M21 | 1 | Upper Torso Back Cover (https://github.com/microsoft/gestureBotDesignKit/blob/main/hardware/3D_Print/gB_UpperTorsoBackCover.stl) | 
M22 | 1 | Upper Torso Front Cover (https://github.com/microsoft/gestureBotDesignKit/blob/main/hardware/3D_Print/gB_UpperTorsoFrontCover.stl) | 
M23 | 1 | Upper Torso Frame (https://github.com/microsoft/gestureBotDesignKit/blob/main/hardware/3D_Print/gB_UpperTorsoFrame.stl) | 

# Step-by-Step Instructions

The 3D-printed parts are used to organize this project's task steps into sessions. 3D printing a part usually requires more time than is reasonable for a work session, often leaving the print operation to complete overnight as the most practical solution.

## Session 1: Set Up the Servo Controller Electronics

In the first session we will begin the process of 3D-printing the gestureBot's plastic parts starting with the base frame while connecting the servo controller to the powered USB3 Hub and a single servo motor.

Session 1 Complete

## Session 2: Configure the Servos

In the second session we will 3D-print the gestureBot's torso components while establishing the communication network for our servo motors by connecting them one-by-one to the PC and using using the Robotis Dynamixel Wizard 2.0 (http://en.robotis.com/service/downloadpage.php?ca_id=10) application to program each with a unique ID.

Session 2 Complete

## Session 3: Assemble the Torso

In the third session we will 3D-print the head components while assembling the gestureBot's torso.

Session 3 Complete

## Session 4: Assemble the Head Structure

In the fourth session we will 3D-print the components for both arms while assembling the structural components of the gestureBot's head.

Session 4 Complete

## Session 5: Assemble the Right Arm

In the fifth session we will 3D-print the base component while assembling the gestureBot's right arm.

## Session 6: Assemble the Left Arm

In the sixth session we will 3D-print the eye and ear components (in an alternate color if desired) while assembling the gestureBot's left arm.

Session 6 Complete

## Session 7: Attach the Arms and Test the Servos

In the seventh session we will 3D-print the hood component (in an alternate color if desired) while we attach the arms to the torso and test the servos using the Robotis Dynamixel Wizard 2.0 (https://www.robotis.us/dynamixel-management/) application.

Session 7 Complete

## Session 8: Complete the Head

In the eigth session we will 3D-print the hands and arm servo covers while we assemble the the head components.

Session 8 Complete

## Session 9: Install the Body Covers

In the ninth session we will 3D-print the torso front and back covers while we install the arm servo covers and hands.

Session 9 Complete

## Session 10: Run the Gesture Applications

In the tenth session we will 3D-print the torso cover components while we attach the hands and the arm servo covers. At this point the gestureBot will be ready to run the Labanotation Suite software applications. The torso covers can be attached as soon as they are finished printing.

Session 10 Complete

# A last word...

Something to keep in mind is that this kit is designed to be changed and adapted. The 3D models are simple and lend themselves to modifications using such tools as Blender (https://www.blender.org/). Additional devices such as cameras, microphones, and loudspeakers can be added using the two available USB ports in the base of the robot, as well as leveraging other devices and connections through the host PC.

We can't wait to see what you come up with!

--the Microsoft Applied Robotics Research Team

Documentation built with MkDocs (https://www.mkdocs.org/).

×Close

#### Search

From here you can search these documents. Enter your search terms below.

×Close

#### Keyboard Shortcuts

Keys | Action
? | Open this help
n | Next page
p | Previous page
s | Search

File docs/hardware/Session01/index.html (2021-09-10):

Microsoft Applied Robotics Research Library: gestureBotDesignKit

- Search
- Microsoft Applied Robotics Research Library
- Open Source Samples for Service Robotics
- gestureBot Construction Guide
- Session 1: Set Up the Servo Controller Electronics
- Next -> Session 2 - Communicate with the Servos

##  Microsoft Applied Robotics Research Library (https://microsoft.github.io/AppliedRoboticsResearchLibrary/)

### Open Source Samples for Service Robotics

 (https://opensource.org/licenses/MIT)

# gestureBot Construction Guide

## Session 1: Set Up the Servo Controller Electronics

In this first session we will begin the process of 3D-printing robot plastic parts starting with the base frame which will be used in Session 2. Then, we will connect the servo controller to the powered USB3 Hub and a single servo motor.

### Parts:

- (2) servos and their included 130mm cables
- USB Terminal Block
- USB3 Hub with Power Supply
- Servo Controller

### Tools:

- wire strippers/cutters
- 2mm screwdriver

Session01 parts and tools

### Procedure:

#### First, start 3D-printing the parts required for the next session:

- Base Frame (https://github.com/microsoft/gestureBotDesignKit/blob/main/hardware/3D_Print/gB_BaseFrame.stl)

#### Second, connect the controller and Terminal Block to the USB Hub:

- From two servo packages, remove the short connection cables and servos then set one servo aside. 2 short cables and servos
- Using the wire strippers/cutters, cut the plastic connector off of one of the short connection cables. cut short cable connector
- Cut the Pin3 wire completely off the remaining connector and save it to use as a ground jumper wire. ground wire cutting Tip: Double check you are cutting the correct wire!
- Using the wire stripper's stranded 22-gauge slot, remove approximately 3mm of the insulation from each end of the ground jumper wire and the remaining two ends of the connector cable. ground wire end stripping
- Using your fingers, twist the wire ends so that the strands hold together. jumper cable preparation ground wire preparation
- Using the 2mm screwdriver, loosen the screw-clamps on the USB terminal block marked 'S', '-', and '+'. USB terminal block preparation USB terminal block preparation end view
- Insert one end of the prepared jumper wire into the USB terminal block's screw clamp marked "-" then tighten with the screw driver. USB terminal block pull-test Tip: Make sure the wire is correctly connected by firmly pulling on it and visually checking that it is not slipping out
- Connect the wires from the short cable to the USB Terminal Block:
- Insert both the loose end of the prepared wire clamped into '-' and the cable wire connected to pin 1 into the wire clamp marked 'S' then tighten with the screwdriver.
- Insert the cable wire connected to pin 2 on the connector into the wire clamp marked "+" (for positive voltage) and tighten with the screwdriver. USB terminal block wiring guide Tip: the jumper wire ties the negative side of the power provided by USB to chassis ground which reduces electromagnetic noise that may interfere with communications between the controller and the servos.
- Connect the USB Terminal Block to the Servo Controller with any one of the four three-pin connectors on the controller. connect servo controller to USB terminal block
- Plug the USB Terminal Block into the USB Hub using the port closest to the hub's link cable. Using the short USB-to-mini cable, connect the servo controller to any of the USB Hub's ports. plug controller into USB hub
- Connect the servo to the servo controller with the remaining 130mm cable. The cable connector must snap into place on either connector on the servo. The other end of the cable can be inserted into any of the three remaining 3-pin connectors on the servo controller PC board. plug cable into servo plug servo into controller Tip: Look closely at the cable connector ends and the receptacles to make sure the pin orientation is correct. If you push hard enough, it is possible to mistakenly insert them backwards. When inserted correctly, they will "snap" into place.

#### Third, power it up!

- Plug the USB Hub's power supply into an AC receptacle and insert its connector into the USB Hub. Observe a LED inside the servo flash red momentarily and a green LED on the controller turn on when power is applied. observe servo red light flash
- Plug the USB Hub into your PC, then use Windows to open Device Manager and note which serial port number the servo controller is assigned to (for example: "COM4") gB_DeviceManager Com Port

## Next -> Session 2 - Communicate with the Servos

Documentation built with MkDocs (https://www.mkdocs.org/).

×Close

#### Search

From here you can search these documents. Enter your search terms below.

×Close

#### Keyboard Shortcuts

Keys | Action
? | Open this help
n | Next page
p | Previous page
s | Search

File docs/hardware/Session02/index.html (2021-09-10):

Microsoft Applied Robotics Research Library: gestureBotDesignKit

- Search
- Microsoft Applied Robotics Research Library
- Open Source Samples for Service Robotics
- gestureBot Construction Guide
- Session 2: Configure the Servos
- Next -> Session 3: Assemble the Torso

##  Microsoft Applied Robotics Research Library (https://microsoft.github.io/AppliedRoboticsResearchLibrary/)

### Open Source Samples for Service Robotics

 (https://opensource.org/licenses/MIT)

# gestureBot Construction Guide

## Session 2: Configure the Servos

In this session we will 3D-print the robot's torso components while establishing the communication network for our servo motors by connecting them one-by-one to the PC and using a software tool to program each with a unique ID. Servo ID Map

### Parts:

- USB hub and power supply, servo, and servo controller assembly from Session 1
- servo set aside in Session 1
- (10) servos and their 130mm cables

### Tools:

- pen and light-colored tape for labeling servo ID's

Session 2 parts and tools Session 2 servos

### Procedure:

#### First, start 3D-printing the parts required for the next session:

- Hip Cover (https://github.com/microsoft/gestureBotDesignKit/blob/main/hardware/3D_print/gB_HipCover.stl)
- Hip Swing Bracket (https://github.com/microsoft/gestureBotDesignKit/blob/main/hardware/3D_print/gB_SwingBracket_Hip.stl)
- Servo Wheel (https://github.com/microsoft/gestureBotDesignKit/blob/main/hardware/3D_print/gBServoWheel.stl)
- Upper Torso Frame (https://github.com/microsoft/gestureBotDesignKit/blob/main/hardware/3D_print/gB_UpperTorsoFrame.stl)
- Servo Wheel (https://github.com/microsoft/gestureBotDesignKit/blob/main/hardware/3D_print/gb_SwingBracket_Hip.stl)
- Servo Mount Plate (https://github.com/microsoft/gestureBotDesignKit/blob/main/hardware/3D_print/gb_UpperTorsoFrame.stl)

Tip: Many 3D-printers have enough room on their build plate to print all of these models at the same time. Follow your printer's software instructions on how to add multiple models to a printing project file.

#### Second, download and install the servo configuration software:

- Download the Robotis Dynamixel Wizard 2.0 software appropriate for you platform from this web page: http://en.robotis.com/service/downloadpage.php?ca_id=10
- Install and launch the Dynamixel Wizard 2.0 application, which provides a Graphical User Interface (GUI) for configuring the servo motors. If needed, installation instructions are provided on the this web page: https://emanual.robotis.com/docs/en/software/dynamixel/dynamixel_wizard2/#introduction
- Select the Options button on the top level menu
- In the Scan section, adjust the following settings:
- select only Protocol 2.0
- select the com port that showed up in Device Manager
- select only 1000000 bps
- leave the other options at default
- select OK

DynamixelWizard2 TopMenu Options

- Select the Scan button on the top level menu. DynamixelWizard2 TopMenu ScanButton
- The scan should find one XL-320 servo at ID:001 in the list on the left side of the GUI,and show a list of the servo's memory page in the center of the GUI. Also, a device listed as Unknown at ID:200 will appear in the list. This represents the servo controller PC board and can be ignored. In the left-side list, select the [ID:001]XL-320 servo node. DynamixelWizard2 TopMenu Select Servo ID:001
- In the memory page list, select and highlight row Address 3, which contains the servo's ID. If the servo is brand new out-of-the-package, it should already be set to Decimal value "1". DynamixelWizard2 TopMenu Select Servo ID Row 3
- When the Address row is selected, a window labeled ID will appear in the lower right corner of the application GUI. In the list of available addresses, select address 2 (Decimal) and then select "Save" below. DynamixelWizard2 TopMenu Set Servo ID UI to 2
- The memory page list should now show the value Decimal 2 in the ID row. DynamixelWizard2 TopMenu Servo Programmed ID2
- In the upper right corner of the UI basic controls for the XL-320 are available. By turning the Torque switch on and then selecting a position on the wheel, the servo horn will rotate to that position. Feel free to try out turning the LED off and on and switching from the Joint to Wheel mode. You will notice that other UI's appear on the right side of the application when different rows are selected in the memory page. For now, don't change any other parameter other than the servo ID. DynamixelWizard2 TopMenu Servo ControlUI Tip: Be sure to return to Joint mode before you finish.
- Label the newly programmed servo as ID:2 with tape and a pen, or return the servo to the bag and label the bag, or whatever method works best for you to identify the servo ID later. label the servo

#### Third, program the servo ID's from 1 to 12:

- Disconnect the labeled servo and repeat the process above until each of the servos has been programmed and labeled with a unique ID from 1 through 12. programmed servos

Tip: Removing the cable from the servo requires significant force, but the Robotis cables are strong and designed for this. Grip the cable between your thumb and the side of your index finger near the servo-side connector and grip the servo with your other hand. Without jerking, pull the cable firmly up and out of the connector.

disconnect servo cable

## Next -> Session 3: Assemble the Torso

Documentation built with MkDocs (https://www.mkdocs.org/).

×Close

#### Search

From here you can search these documents. Enter your search terms below.

×Close

#### Keyboard Shortcuts

Keys | Action
? | Open this help
n | Next page
p | Previous page
s | Search

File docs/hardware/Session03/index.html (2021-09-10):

Microsoft Applied Robotics Research Library: gestureBotDesignKit

- Search
- Microsoft Applied Robotics Research Library
- Open Source Samples for Service Robotics
- gestureBot Construction Guide
- Session 3: Assemble the Torso
- Next -> Session 4: Assemble the Head Structure

##  Microsoft Applied Robotics Research Library (https://microsoft.github.io/AppliedRoboticsResearchLibrary/)

### Open Source Samples for Service Robotics

 (https://opensource.org/licenses/MIT)

# gestureBot Construction Guide

## Session 3: Assemble the Torso

In this session we will 3D-print the head components while assembling the gestureBot's torso.

### Parts:

- (3) servos labeled ID:004, ID:003, and ID:002 programmed in Session 2
- (4) 130MM servo cables
- (22) short plastic rivets
- (5) long plastic rivets
- (4) 3mm miniature steel screws
- Base Frame (https://github.com/microsoft/gestureBotDesignKit/blob/main/hardware/3D_Print/gB_BaseFrame.stl) 3D-printed in Session 1, the base frame is the lower torso component and provides the stationary mounting point for servo ID:004 and anchors all of the moving parts of the gestureBot.
- Hip Cover (https://github.com/microsoft/gestureBotDesignKit/blob/main/hardware/3D_print/gb_HipCover.stl) 3D-printed in Session 2, the hip cover attaches to the base frame and it's spherical shape allows the gestureBot's hip joint to move without exposing its interior.
- Hip Swing Bracket (https://github.com/microsoft/gestureBotDesignKit/blob/main/hardware/3D_print/gb_SwingBracket_Hip.stl) 3D-printed in Session 2, the hip swing bracket and servo wheel attach to servo ID:004 and ID:003 rotating vertically to allow the entire gestureBot to lean forward and backward.
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

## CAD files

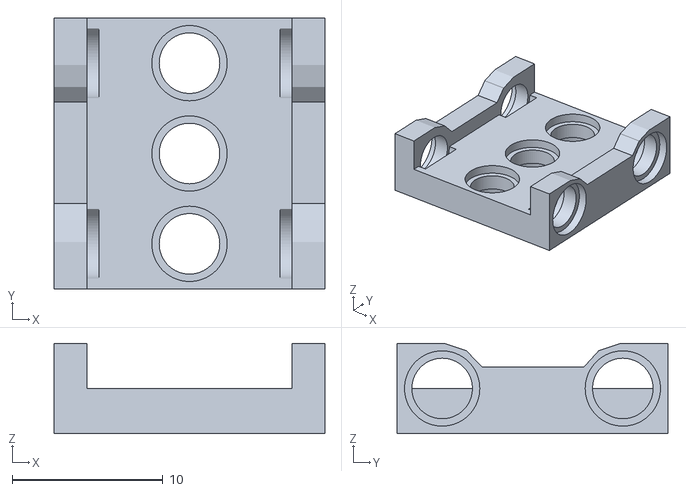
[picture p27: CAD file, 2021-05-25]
docs/hardware/3D_Print/gB_ServoMountPlate.stl
18.0 x 18.0 x 6.00

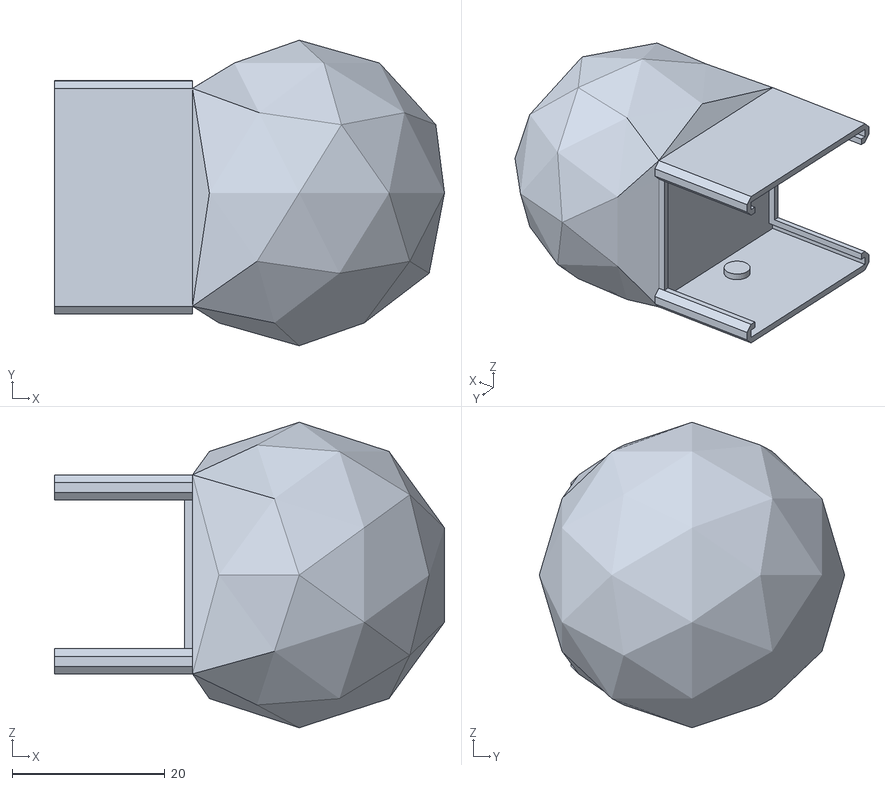
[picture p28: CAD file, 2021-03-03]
docs/hardware/3D_Print/gB_Hand.stl
51.1 x 40.0 x 40.0

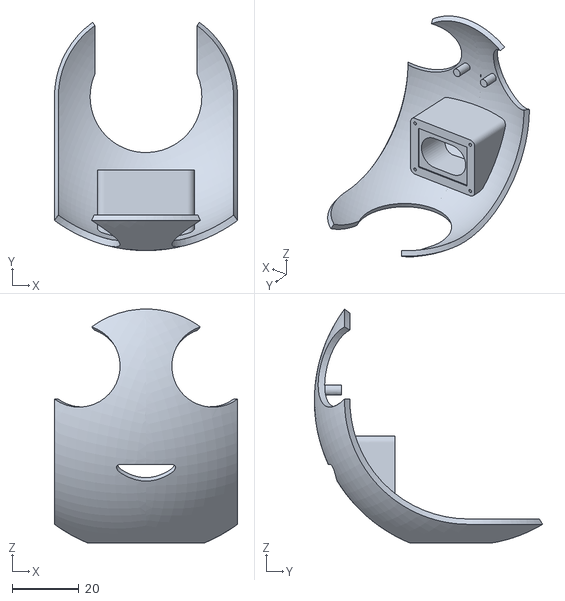
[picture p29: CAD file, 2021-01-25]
docs/hardware/3D_Print/gB_Face.STL
54.9 x 68.5 x 70.1

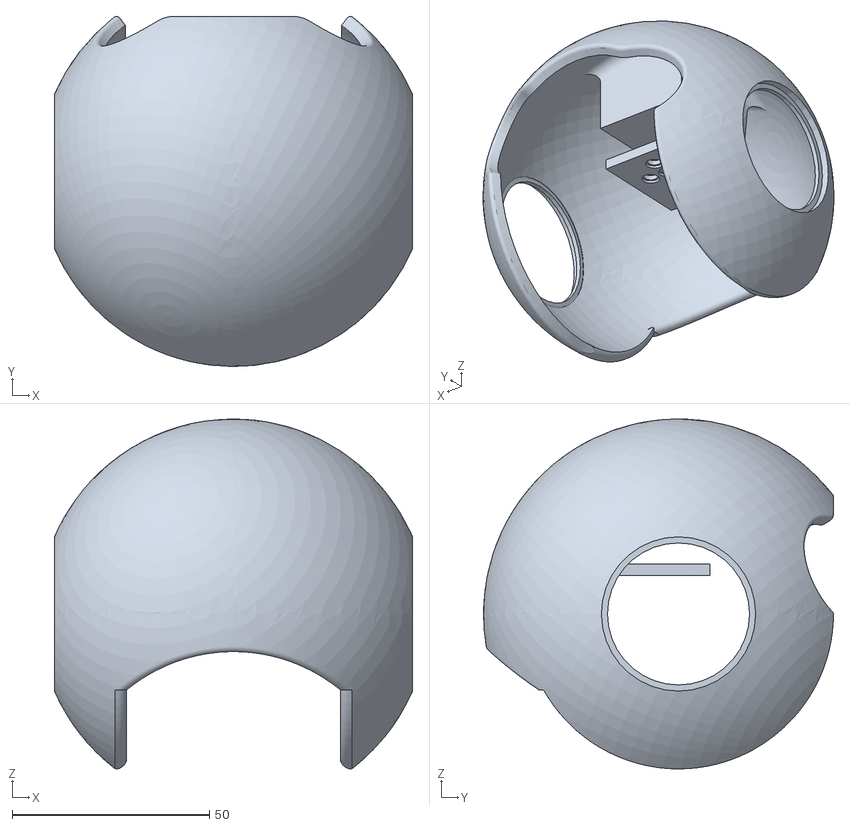
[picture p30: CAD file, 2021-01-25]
docs/hardware/3D_Print/gB_Hood.stl
90.8 x 88.7 x 88.7

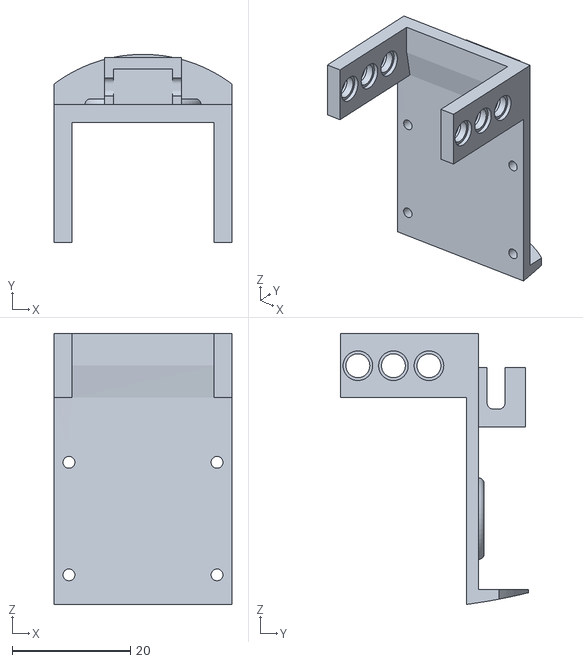
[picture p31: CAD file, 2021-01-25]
docs/hardware/3D_Print/gB_HeadFrame.stl
30.0 x 31.8 x 45.8

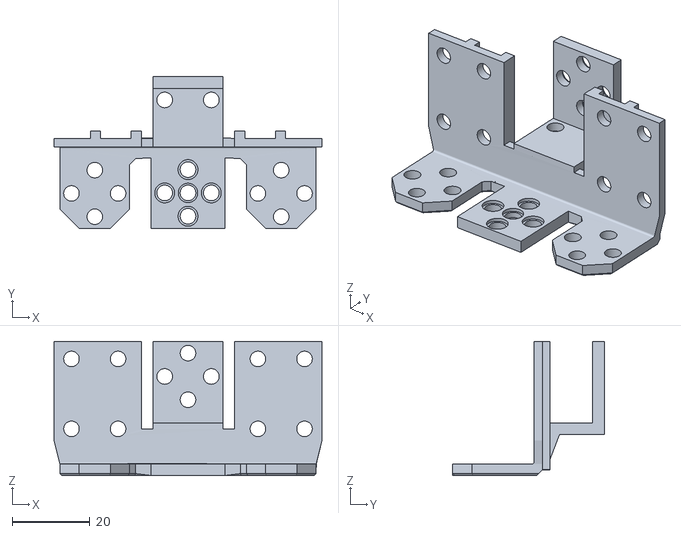
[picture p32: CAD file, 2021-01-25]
docs/hardware/3D_Print/gB_UpperTorsoFrame.stl
69.0 x 39.1 x 34.5

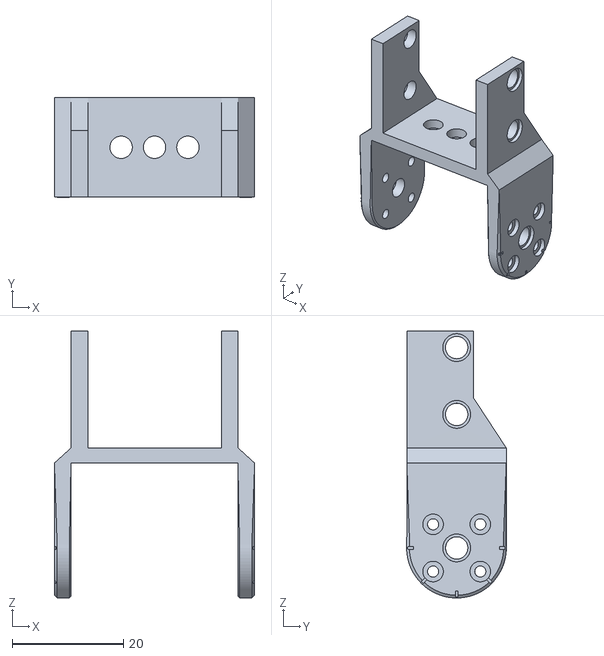
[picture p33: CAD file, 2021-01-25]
docs/hardware/3D_Print/gB_SwingBracket_Hip.stl
36.0 x 17.9 x 48.0

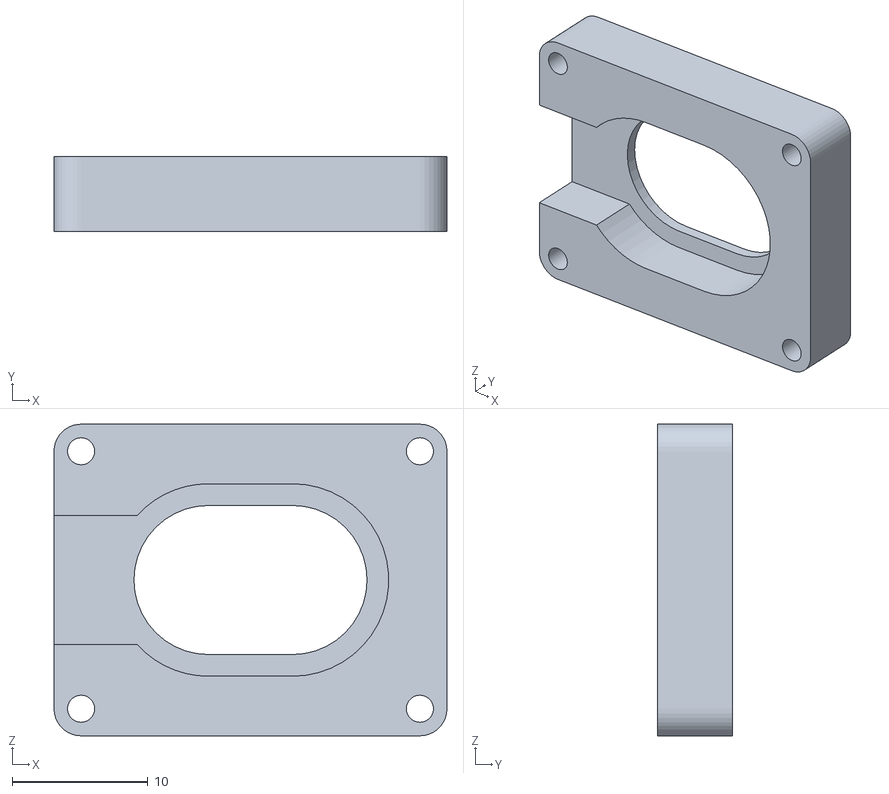
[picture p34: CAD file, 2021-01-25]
docs/hardware/3D_Print/gB_Speaker.stl
29.0 x 5.50 x 23.0

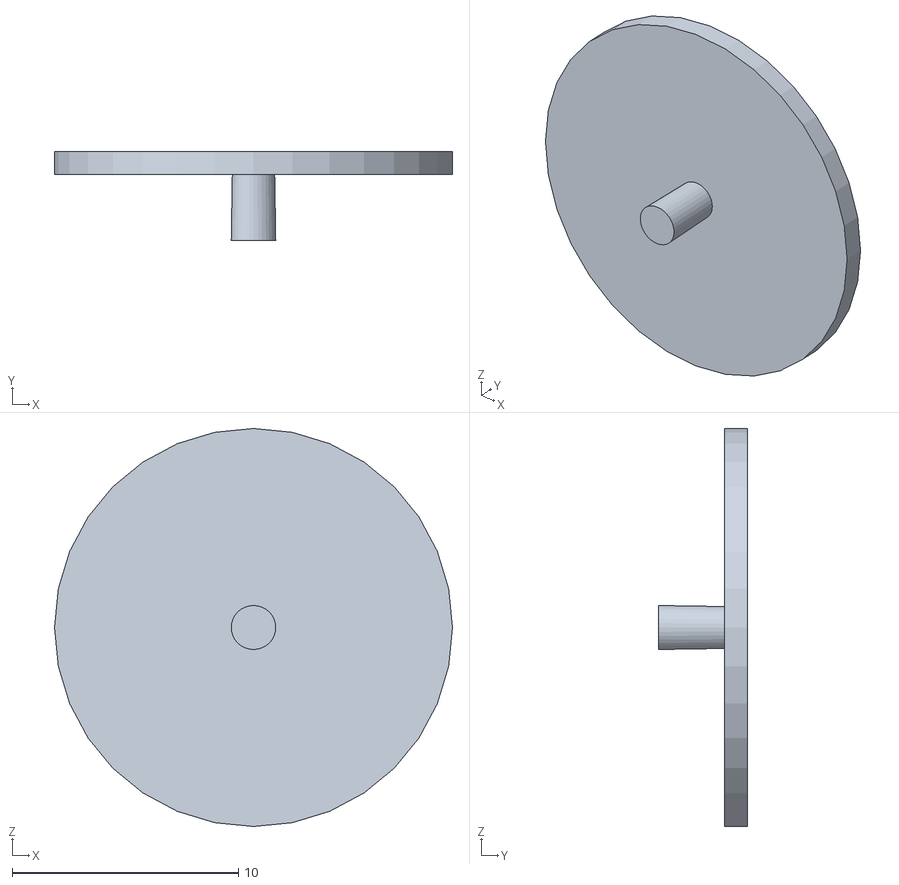
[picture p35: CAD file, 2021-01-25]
docs/hardware/3D_Print/gB_BracketCover_RivetSide.stl
17.6 x 3.93 x 17.6

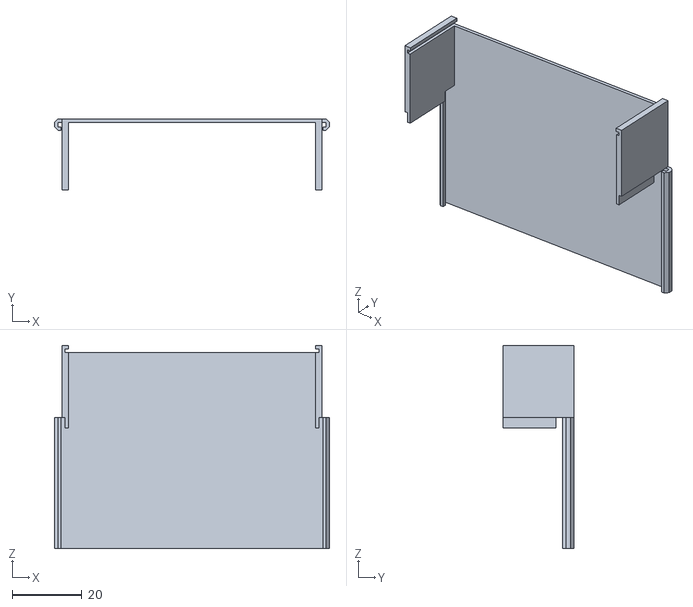
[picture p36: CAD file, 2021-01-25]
docs/hardware/3D_Print/gB_UpperTorsoBackCover.stl
79.1 x 20.5 x 58.4

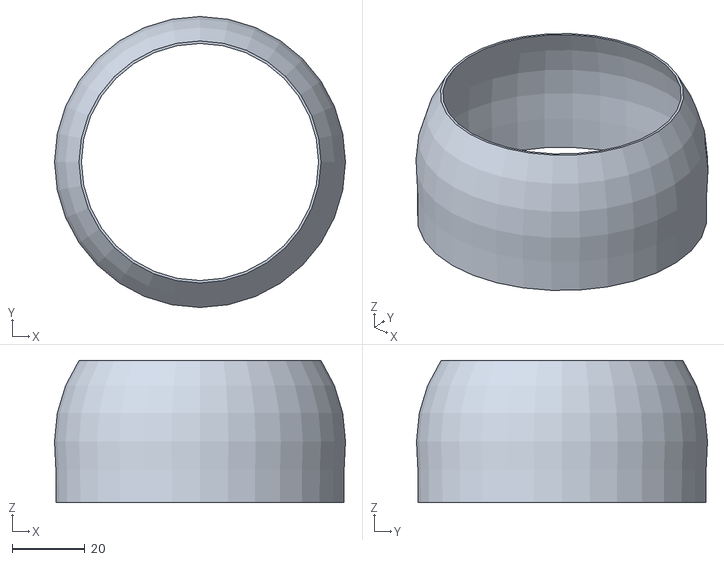
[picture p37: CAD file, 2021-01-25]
docs/hardware/3D_Print/gB_HipCover.stl
80.0 x 80.0 x 39.1

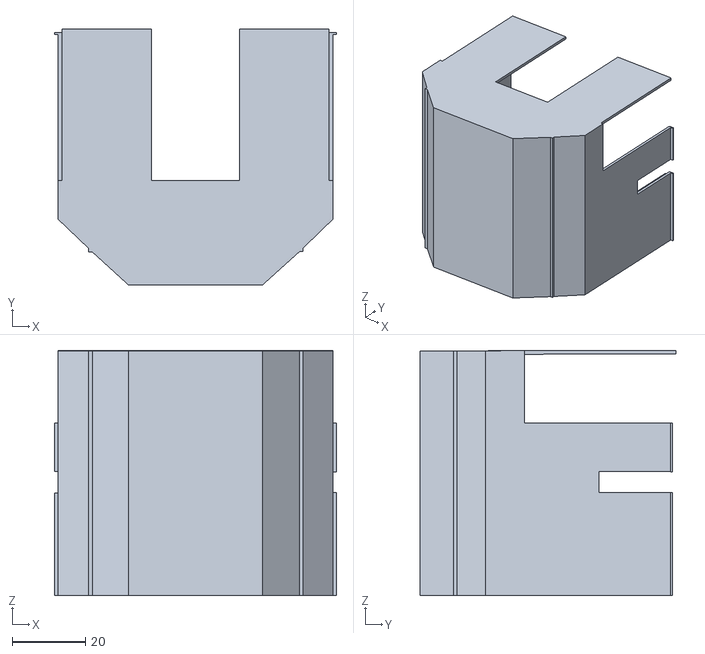
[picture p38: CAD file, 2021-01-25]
docs/hardware/3D_Print/gB_UpperTorsoFrontCover.stl
77.0 x 70.0 x 66.9

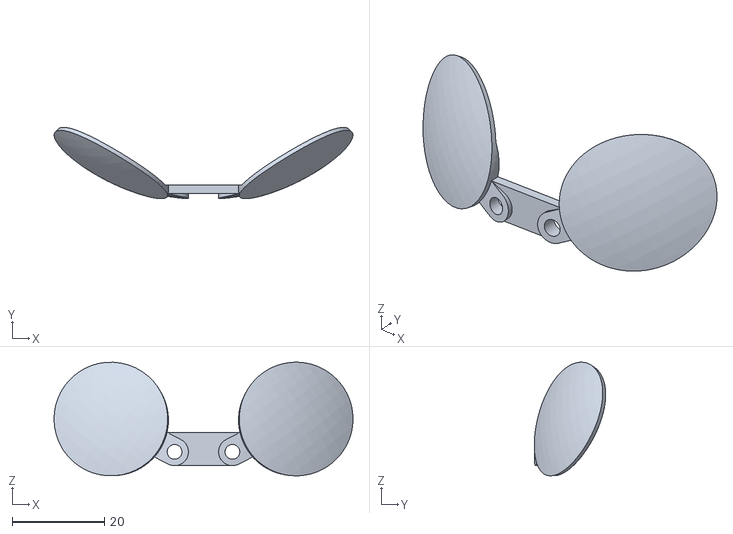
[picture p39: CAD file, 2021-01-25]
docs/hardware/3D_Print/gB_Eyes.STL
64.9 x 15.5 x 24.7

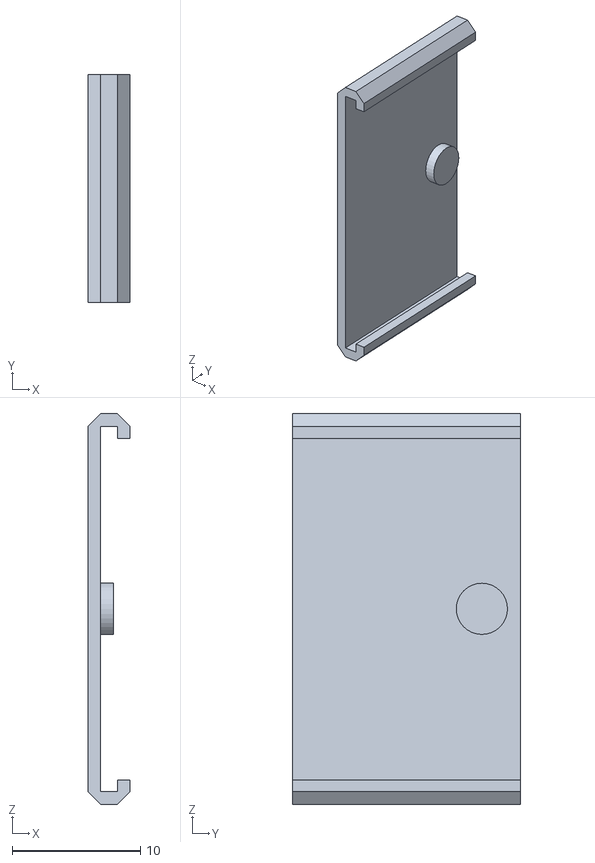
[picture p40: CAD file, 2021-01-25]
docs/hardware/3D_Print/gB_ServoSideCover.stl
3.31 x 17.8 x 30.5

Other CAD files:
docs/hardware/3D_Print/gB_BaseFrame.stl
docs/hardware/3D_Print/gB_Base.stl
docs/hardware/3D_Print/gB_SwingBracket_Head.stl
docs/hardware/3D_Print/gB_ServoCover.stl
docs/hardware/3D_Print/gB_BracketCover_ScrewSide.stl
docs/hardware/3D_Print/gB_Ear.STL
docs/hardware/3D_Print/gB_Neck.stl
docs/hardware/3D_Print/gB_ServoWheel.stl
docs/hardware/3D_Print/gB_SwingBracket_ScrewMount.stl

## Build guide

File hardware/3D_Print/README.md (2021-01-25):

# gestureBot 3D-Print Files

This folder contains 3D-printable files for building the plastic components of your gestureBot. The models are exported from the Blender file **gestureBot.blend** in the parent folder.  Ultimaker3-compatible component sets are provided in the **.gcode** format. For other 3D-printers, models of individual robot components are provided in the **.stl** format.

## Ultimaker3 Component Sets
### UM3_gB_Base_Set.gcode
- (x1) gB_Base
### UM3_gB_BaseFrame_Set.gcode
- (x1) gB_BaseFrame
### UM3_gB_Torso_Set.gcode
- (x1) GB_UpperTorsoFrame
- (x3) GB_ServoMountPlate
- (x1) GB_ServoWheel
- (X1) GB_SwingBracket_RivetMount
### UM3_gB_HeadFrame_Set.gcode
- (x1) gB_SwingBracket_Head
- (x1) gB_ServoWheel
- (x1) gB_Neck
- (x1) gB_FaceFrame
### UM3_gB_ArmFrame_Set.gcode
- (x4) gB_SwingBracket_ScrewMount
- (x4) gB_ServoWheel
- (x2) gB_ServoMountPlate
### UM3_gB_Face_Set.gcode
- (x1) gB_Face
- (x1) gB_SpeakerFrame
### UM3_gB_EyesEars_Set.gcode
- (x1) gB_Eyes
- (x2) gB_Ear
### UM3_gB_Hood_Set.gcode
- (x1) gB_Hood
### UM3_Hand_Set
- (x2) gB_Hand
### UM3_gB_ArmCover_Set
- (x2) gB_ShoulderCover
- (x2) gB_ArmCover
- (x2) gB_ElbowCover
### UM3_gB_FrontCover_Set
- (x1) gB_FrontCover
### UM3_gB_BackCover_Set
- (x1) gB_BackCover

## Individual Components
- gB_Base.stl (x1)
- gB_BaseFrame.stl (x1)
- gB_BracketCover_RivetSide.stl (x4)
- gB_BracketCover_ScrewSide.stl (x4)
- gB_Ear.stl (x2)
- gB_Eyes.stl (x1)
- gB_Face.stl (x1)
- gB_Hand.stl (x2)
- gB_HeadFrame.stl (x1)
- gB_HipCover.stl (x1)
- gB_Hood.stl (x1)
- gB_Neck.stl (x1)
- gB_ServoCover.stl (x6)
- gB_ServoMountPlate.stl (x5)
- gB_ServoSideCover.stl (x6)
- gB_ServoWheel.stl (x6)
- gB_Speaker.stl (x1)
- gB_SwingBracket_Head.stl (x1)
- gB_SwingBracket_Hip.stl (x1)
- gB_SwingBracket_ScrewMount.stl (x4)
- gB_UpperTorso_BackCover.stl (x1)
- gB_UpperTorsoFrame.stl (x1)
- gB_UpperTorso_FrontCover.stl (x1)

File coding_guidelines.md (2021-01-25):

# Modern Python Coding Guidelines
- Runs under Python3
- 3-space indents

# Modern C++ Coding Guidelines

We are using Modern C++11. Smart pointers, Lambdas, and C++11 multithreading primitives are your friend.

## Quick Note

The great thing about "standards" is that there are many to chose from: [ISO](https://isocpp.org/wiki/faq/coding-standards), [Sutter &amp; Stroustrup](https://github.com/isocpp/CppCoreGuidelines/blob/master/CppCoreGuidelines.md), [ROS](http://wiki.ros.org/CppStyleGuide), [LINUX](https://www.kernel.org/doc/Documentation/CodingStyle), [Google's](https://google.github.io/styleguide/cppguide.html), [Microsoft's](https://msdn.microsoft.com/en-us/library/888a6zcz.aspx), [CERN's](http://atlas-computing.web.cern.ch/atlas-computing/projects/qa/draft_guidelines.html), [GCC's](https://gcc.gnu.org/wiki/CppConventions), [ARM's](http://infocenter.arm.com/help/index.jsp?topic=/com.arm.doc.dui0475c/CJAJAJCJ.html), [LLVM's](http://llvm.org/docs/CodingStandards.html) and probably 
thousands of others. Unfortunately most of these can't even agree on something as basic as how to name a class or a constant. This is probably due to the fact that these standards often carry lots of  legacy issues due to supporting existing code bases. The intention behind this document is to create guidance that remains as close to ISO, Sutter &amp; Stroustrup and ROS while resolving as many conflicts, disadvantages and inconsistencies as possible among them.

## Naming Conventions

Avoid using any sort of Hungarian notation on names and "_ptr" on pointers.

| **Code Element** | **Style** | **Comment** |
| --- | --- | --- |
| Namespace | under\_scored | Differentiate from class names |
| Class name | CamelCase | To differentiate from STL types which ISO recommends (do not use "C" or "T" prefixes) |
| Function name | camelCase | Lower case start is almost universal except for .Net world |
| Parameters/Locals | under\_scored | Vast majority of standards recommends this because \_ is more readable to C++ crowd (although not much to Java/.Net crowd) |
| Member variables | under\_scored\_with\_ | The prefix \_ is heavily discouraged as ISO has rules around reserving \_identifiers, so we recommend suffix instead |
| Enums and its members | CamelCase | Most except very old standards agree with this one |
| Globals | g\_under\_scored | You shouldn't have these in first place! |
| Constants | UPPER\_CASE | Very contentious and we just have to pick one here, unless if is a private constant in class or method, then use naming for Members or Locals |
| File names | Match case of class name in file | Lot of pro and cons either way but this removes inconsistency in auto generated code (important for ROS) |

## Header Files

Use a namespace qualified #ifdef to protect against multiple inclusion:

```
#ifndef msr_airsim_MyHeader_hpp
#define msr_airsim_MyHeader_hpp

//--your code

#endif
```

The reason we don't use #pragma once is because it's not supported if same header file exists at multiple places (which might be possible under ROS build system!).

## Bracketing

Inside function or method body place curly bracket on same line. 
Outside that the Namespace, Class and methods levels use separate line.
This is called [K&amp;R style](https://en.wikipedia.org/wiki/Indent_style#K.26R_style) and its variants are widely used in C++ vs other styles which are more popular in other languages. 
Notice that curlies are not required if you have single statement, but complex statements are easier to keep correct with the braces.

```
int main(int argc, char* argv[])
{
     while (x == y) {
        f0();
        if (cont()) {
            f1();
        } else {
            f2();
            f3();
        }
        if (x > 100)
            break;
    }
}
```

## Const and References

Religiously review all non-scalar parameters you declare to be candidate for const and references. If you are coming from languages such as C#/Java/Python,
the most often mistake you would make is to pass parameters by value instead of `const T&;` Especially most of the strings, vectors and maps you want to 
pass as `const T&;` (if they are readonly) or `T&` (if they are writable). Also add `const` suffix to methods as much as possible.

## Overriding
When overriding virtual method, use override suffix.

## Pointers

This is really about memory management.  A simulator has much performance critical code, so we try and avoid overloading the memory manager
with lots of calls to new/delete.  We also want to avoid too much copying of things on the stack, so we pass things by reference when ever possible.
But when the object really needs to live longer than the call stack you often need to allocate that object on
the heap, and so you have a pointer.  Now, if management of the lifetime of that object is going to be tricky we recommend using 
[C++ 11 smart pointers](https://cppstyle.wordpress.com/c11-smart-pointers/). 
But smart pointers do have a cost, so don’t use them blindly everywhere.  For private code 
where performance is paramount, raw pointers can be used.  Raw pointers are also often needed when interfacing with legacy systems
that only accept pointer types, for example, sockets API.  But we try to wrap those legacy interfaces as
much as possible and avoid that style of programming from leaking into the larger code base.  

Religiously check if you can use const everywhere, for example, `const float * const xP`. Avoid using prefix or suffix to indicate pointer types in variable names, i.e. use `my_obj` instead of `myobj_ptr` except in cases where it might make sense to differentiate variables better, for example, `int mynum = 5; int* mynum_ptr = mynum;`

## This is Too Short, ye?

Yes, and it's on purpose because no one likes to read 200 page coding guidelines. The goal here is to cover only most significant things which are 
already not covered by [strict mode compilation in GCC](http://shitalshah.com/p/how-to-enable-and-use-gcc-strict-mode-compilation/) and Level 4 
warnings-as-errors in VC++. If you had like to know about how to write better code in C++, please see [GotW](https://herbsutter.com/gotw/) 
and [Effective Modern C++](http://shop.oreilly.com/product/0636920033707.do) book.

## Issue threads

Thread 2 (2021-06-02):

Bug:  Hood mount needs to use long rivets

davidbaumert, 2021-06-02:
When mounting the hood to the head bracket, the instructions indicate that the short rivets should be used.
Using the short rivets is unacceptably difficult. Using the long rivets work just as well and are much easier to install.
Documentation should be changed.

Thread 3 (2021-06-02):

Bug: documentation repeats servo connection step

davidbaumert, 2021-06-02:
In the construction guide, there are two places where it instructs to connect Servo9 to Servo10.
The second place in the instructions should be removed.

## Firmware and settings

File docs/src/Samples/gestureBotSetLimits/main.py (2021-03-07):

# --------------------------------------------------------------------------------------------
# Copyright (c) Microsoft Corporation. All rights reserved.
# Licensed under the MIT License.
# --------------------------------------------------------------------------------------------

import sys
import os
import threading
import time

from dynamixel_sdk import *                    # Uses Dynamixel SDK library

sys.path.append(os.path.join(os.path.dirname(__file__), '..', '..', 'Libraries'))
import Common.settings as settings

# Protocol version
PROTOCOL_VERSION            = 2.0               # protocol version to be used with the Dynamixel servos

# Control table address

# -------- EEPROM -------------
XL320_CW_ANGLE_LIMIT   = 6
XL320_CCW_ANGLE_LIMIT  = 8

# -------- RAM ----------------
XL320_TORQUE_ENABLE    = 24  # servo mode on/off - turn into wheel
XL320_LED              = 25
XL320_GOAL_POSITION    = 30
XL320_GOAL_VELOCITY    = 32
XL320_GOAL_TORQUE      = 35
XL320_PRESENT_POSITION = 37  # current servo angle
XL320_PRESENT_SPEED    = 39  # current speed
XL320_PESENT_LOAD      = 41  # current load
XL320_PESENT_VOLTAGE   = 45  # current voltage
XL320_PESENT_TEMP      = 46  # current temperature
XL320_MOVING           = 49
XL320_HW_ERROR_STATUS  = 50
XL320_PUNCH            = 51

TORQUE_ENABLE               = 1                 # Value for enabling the torque
TORQUE_DISABLE              = 0                 # Value for disabling the torque

# -----------------------------------------------------------------------------
#
class application:
    #------------------------------------------------------------------------------
    # Class initialization
    #
    def __init__(self):
        self.comPort = "com7"
        self.baudrate = 1000000           # Dynamixel default baudrate : 57600
        self.packetHandler = PacketHandler(PROTOCOL_VERSION)
        self.portHandler = None

        self.servoMap = { 'head': 1, 'neck': 2, 'torso': 3, 'hip': 4, 'rshoulder': 5, 'rarm': 6, 'relbow': 7, 'rhand': 8, 'lshoulder': 9, 'larm': 10, 'lelbow': 11, 'lhand': 12 }

    #------------------------------------------------------------------------------
    #
    def handleError(self, DXL_ID, dxl_comm_result, dxl_error, context):
        if dxl_comm_result != COMM_SUCCESS:
            print(context + " failed: %s" % self.packetHandler.getTxRxResult(dxl_comm_result))
            return False
        elif dxl_error != 0:
            if (dxl_error == 128):
                return self.readHardwareErrorStatus(DXL_ID, context)
            else:
                print(context + " failed: %s" % self.packetHandler.getRxPacketError(dxl_error))
                return False

        return True

    #------------------------------------------------------------------------------
    #
    def readHardwareErrorStatus(self, DXL_ID, context):
        # Read hardware error status
        dxl_hw_error_status, dxl_comm_result, dxl_error = self.packetHandler.read2ByteTxRx(self.portHandler, DXL_ID, XL320_HW_ERROR_STATUS)
        if dxl_comm_result != COMM_SUCCESS:
            print(context + " failed: %s" % self.packetHandler.getTxRxResult(dxl_comm_result))
            return False
        elif dxl_error != 0:
            if (dxl_error == 128):
                if (dxl_hw_error_status != 0x1e04): # exception for gestureBot. see Documentation
                    print(context + " failed: hardware error status: " + hex(dxl_hw_error_status))
                    return False
            else:
                print(context + " failed: %s" % self.packetHandler.getRxPacketError(dxl_error))
                return False

        return True

    # -----------------------------------------------------------------------------
    #
    def connect(self):
        self.disconnect()

        print("gestureBot: connecting to port '" + str(self.comPort) + "'...")

        portHandler = PortHandler(self.comPort)
        success = portHandler.openPort()
        if (not success):
            print("gestureBot: Failed to open port '" + str(self.comPort) + "'.")
            return False

        # Set port baudrate
        success = portHandler.setBaudRate(self.baudrate)
        if (not success):
            print("gestureBot: Failed to set com port baud rate.")
            return False

        # port is ready
        self.portHandler = portHandler

        return True

    # -----------------------------------------------------------------------------
    #
    def disconnect(self):
        if (self.portHandler is None):
            return

        print("gestureBot: disconnecting from port '" + str(self.comPort) + "'...")

        # Close port
        self.portHandler.closePort()
        self.portHandler = None

    #------------------------------------------------------------------------------
    #
    def reboot(self, DXL_ID):
        if (self.portHandler is None):
            return False

        # Dynamixel LED will flicker while it reboots
        dxl_comm_result, dxl_error = self.packetHandler.reboot(self.portHandler, DXL_ID)
        return self.handleError(DXL_ID, dxl_comm_result, dxl_error, "reboot")

    # -----------------------------------------------------------------------------
    #
    def readTxRx(self, DXL_ID, address, numBytes, context):
        if (self.portHandler is None):
            return False

        retries = 0
        while (True):
            if (numBytes == 1):
                data, dxl_comm_result, dxl_error = self.packetHandler.read1ByteTxRx(self.portHandler, DXL_ID, address)
            elif (numBytes == 2):
                data, dxl_comm_result, dxl_error = self.packetHandler.read2ByteTxRx(self.portHandler, DXL_ID, address)
            elif (numBytes == 4):
                data, dxl_comm_result, dxl_error = self.packetHandler.read4ByteTxRx(self.portHandler, DXL_ID, address)

            if (dxl_comm_result == -1000):
                time.sleep(0.1)
                retries = retries + 1
                if (retries > 3):
                    break
            else:
                break

        success = self.handleError(DXL_ID, dxl_comm_result, dxl_error, context)

        return data

    # -----------------------------------------------------------------------------
    #
    def writeTxRx(self, DXL_ID, address, data, numBytes, context):
        if (self.portHandler is None):
            return False

        retries = 0
        while (True):
            if (numBytes == 1):
                dxl_comm_result, dxl_error = self.packetHandler.write1ByteTxRx(self.portHandler, DXL_ID, address, data)
            elif (numBytes == 2):
                dxl_comm_result, dxl_error = self.packetHandler.write2ByteTxRx(self.portHandler, DXL_ID, address, data)
            elif (numBytes == 4):
                dxl_comm_result, dxl_error = self.packetHandler.write4ByteTxRx(self.portHandler, DXL_ID, address, data)

            if (dxl_comm_result == -1000):
                time.sleep(0.1)
                retries = retries + 1
                if (retries > 3):
                    break
            else:
                break

        success = self.handleError(DXL_ID, dxl_comm_result, dxl_error, context)

        return success

    # -----------------------------------------------------------------------------
    #
    def torqueOn(self, DXL_ID):
        return self.writeTxRx(DXL_ID, XL320_TORQUE_ENABLE, TORQUE_ENABLE, 1, "torqueOn")

    # -----------------------------------------------------------------------------
    #
    def torqueOff(self, DXL_ID):
        return self.writeTxRx(DXL_ID, XL320_TORQUE_ENABLE, TORQUE_DISABLE, 1, "torqueOff")

    # -----------------------------------------------------------------------------
    # 
    def setCWAngleLimit(self, DXL_ID, angle):
        if (self.portHandler is None):
            return False

        data_write = [DXL_LOBYTE(angle), DXL_HIBYTE(angle)]
        # dxl_comm_result = self.packetHandler.regWriteTxOnly(self.portHandler, DXL_ID, XL320_CW_ANGLE_LIMIT, 2, data_write)
        dxl_comm_result = self.packetHandler.writeTxOnly(self.portHandler, DXL_ID, XL320_CW_ANGLE_LIMIT, 2, data_write)
        dxl_error = 0

        success = self.handleError(DXL_ID, dxl_comm_result, dxl_error, "CWAngleLimit")

        return success

    # -----------------------------------------------------------------------------
    #
    def setCCWAngleLimit(self, DXL_ID, angle):
        if (self.portHandler is None):
            return False

        data_write = [DXL_LOBYTE(angle), DXL_HIBYTE(angle)]
        # dxl_comm_result = self.packetHandler.regWriteTxOnly(self.portHandler, DXL_ID, XL320_CCW_ANGLE_LIMIT, 2, data_write)
        dxl_comm_result = self.packetHandler.writeTxOnly(self.portHandler, DXL_ID, XL320_CCW_ANGLE_LIMIT, 2, data_write)
        dxl_error = 0

        success = self.handleError(DXL_ID, dxl_comm_result, dxl_error, "CCWAngleLimit")

        return success

    # -----------------------------------------------------------------------------
    # 
    def setAngleLimits(self, DXL_ID, angleCW, angleCCW):
        _angleCW = self.convertAngle(angleCW)
        print("ID: " + str(DXL_ID) + ": setting CW angle limit to " + str(angleCW) + " (" + str(_angleCW) + ")")
        self.setCWAngleLimit(DXL_ID, _angleCW)
        time.sleep(0.1)

        _angleCCW = self.convertAngle(angleCCW)
        print("ID: " + str(DXL_ID) + ": setting CCW angle limit to " + str(angleCCW) + " (" + str(_angleCCW) + ")")
        self.setCCWAngleLimit(DXL_ID, _angleCCW)
        time.sleep(0.1)

    # -----------------------------------------------------------------------------
    # 
    def convertAngle(self, angle):
        #
        # map angle to xl-320 servo range
        while (angle < 0.0):
            angle = angle + 360.0

        while (angle >= 360.0):
            angle -= 360

        if (angle > 180.0):
            angle -= 360.0

        # clamp to servo range
        angle = angle + 150.0
        if (angle > 300.0):
            angle = 300
        elif (angle < 0.0):
            angle = 0

        # convert to position value of destination
        return int(angle/300*1023)

    #------------------------------------------------------------------------------
    #
    def run(self):
        if (not self.connect()):
            return

        for key in self.servoMap:
            self.torqueOff(self.servoMap[key])

        # head
        self.setAngleLimits(1, -70, 50)

        # neck
        self.setAngleLimits(2, -91, 91) # 204..818

        self.disconnect()

#------------------------------------------------------------------------------
#
# main code
#
if __name__ == '__main__':
    # initialize global variables
    settings.initialize()

    # create main application object, then run it
    settings.application = application()
    settings.application.run()

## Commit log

2021-01-25 initial upload
    [gB_Base.stl, gB_BaseFrame.stl, gB_BracketCover_RivetSide.stl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]
2021-03-03 update model assets
    [gB_Hand.stl]
2021-05-25 update servo mount plate model, logo image folder
    [gB_ServoMountPlate.stl]
2021-09-10 fix typo and comment
    [main.py]
2021-09-10 update mkdocs config to use main branch
    [gB_Base.stl, gB_BaseFrame.stl, gB_BracketCover_RivetSide.stl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]

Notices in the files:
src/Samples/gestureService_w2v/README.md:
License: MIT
